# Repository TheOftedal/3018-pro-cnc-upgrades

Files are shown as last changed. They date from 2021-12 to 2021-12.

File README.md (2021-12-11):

# SainSmart Genmitsu 3018-PRO X-Axis Limit Switch

X-axis limiter based on two sub miniature leaf spring switches to sense when the spindle has reached the edge of the x-axis.
This leaves only a couple of millimeters to the edge of the x-axis on either side.
The switches are mounted to the frame with the original M5x16 screws and can thus be fitted with no manipulation of the frame.

## Files

This design consists of two files; x-axis-limit-switch-left and x-axis-limit-switch-right. These pieces are near identical but the right switch has a 2mm longer extrusion to accompany for the stepper motor screws.

## Parts

### Switch

The limit switch holder is designed around a sub miniature leaf spring switch with dimensions of approx. 6.5 x 12.8 x 5.8mm.
Example model that should fit this design: [CYT1073](https://www.amazon.com/Cylewet-25Pcs-Switch-Arduino-CYT1073/dp/B073TYWX86).

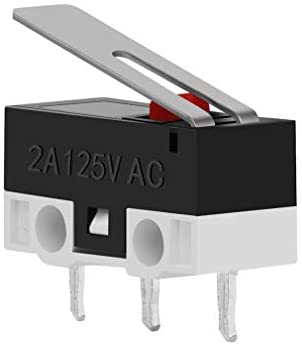
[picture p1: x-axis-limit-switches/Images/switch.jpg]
Switch


### Cables

Any pair of low power cables should suffice for this application.
I do however recommend using a maximum cable dimension of 1.5mm2 to make it easier to solder them onto the micro switch contacts.

### Connectors

The original Genmitsu 3018-PRO control board has a standard dupont pinout for the limit switch connectors and it is therefore recommended to use a dupont crimping tool and 2-pin female connectors to connect the switches to the control board.

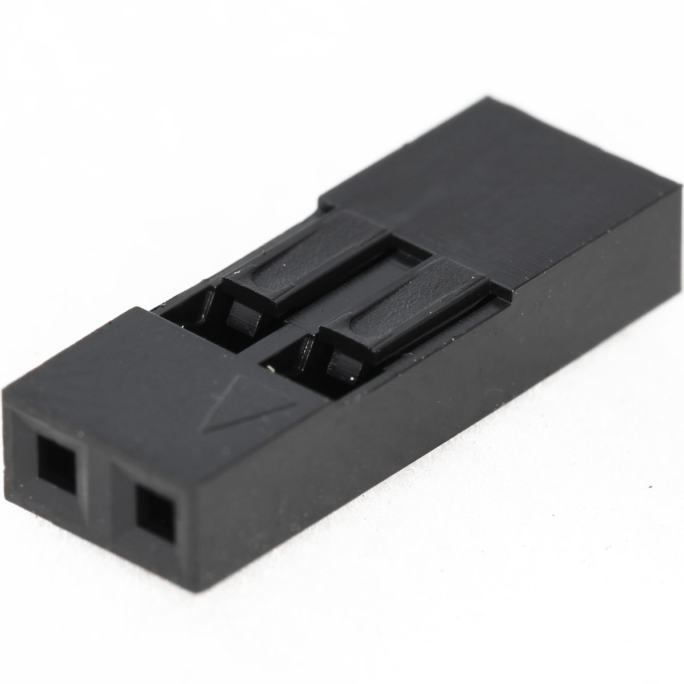
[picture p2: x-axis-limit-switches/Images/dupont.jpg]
Switch


## How to

### Step 1 - 3D-print the holders

Print both 'x-axis-limit-switch-left' and 'x-axis-limit-switch-right' with your choice of printer and filament.

I have successfully printed the design with PLA and with the following settings:

- Extruder Temperature: 230c
- Platform Temperature: 50c
- Layer Height: 0.18mm
- First Layer Height: 0.22mm
- Infill: 15%
- Raft: No
- Supports: No

Due to printing without supports there may be some stringing in the screw holes but this can be easily scraped out with a knife.

### Step 2 - Solder the switches

Solder the cables to the C (Common) and NO (Normally Open) pins of the switch. I recommend to place a small piece of shrink tubing over the solder joints to avoid shortint the pins.

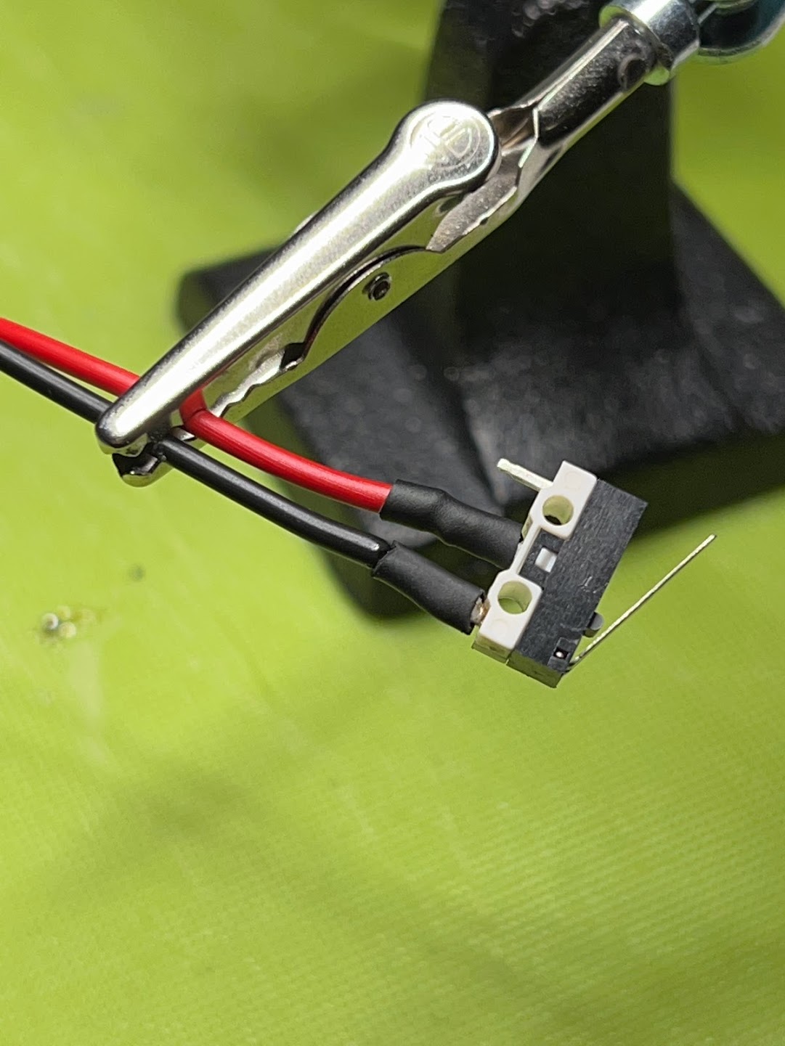
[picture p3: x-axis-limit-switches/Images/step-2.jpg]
Soldering


### Step 3 - Mount the switches to the 3D-printed holders

Fit the cables and switches through the hole of the 3D-printed holders making sure the switch leaf spring is pointing downwards.
The switch should snap into place and be helt snuggly by friction. If the switch is loose, apply some superglue to the switch before fitting it in the socket.

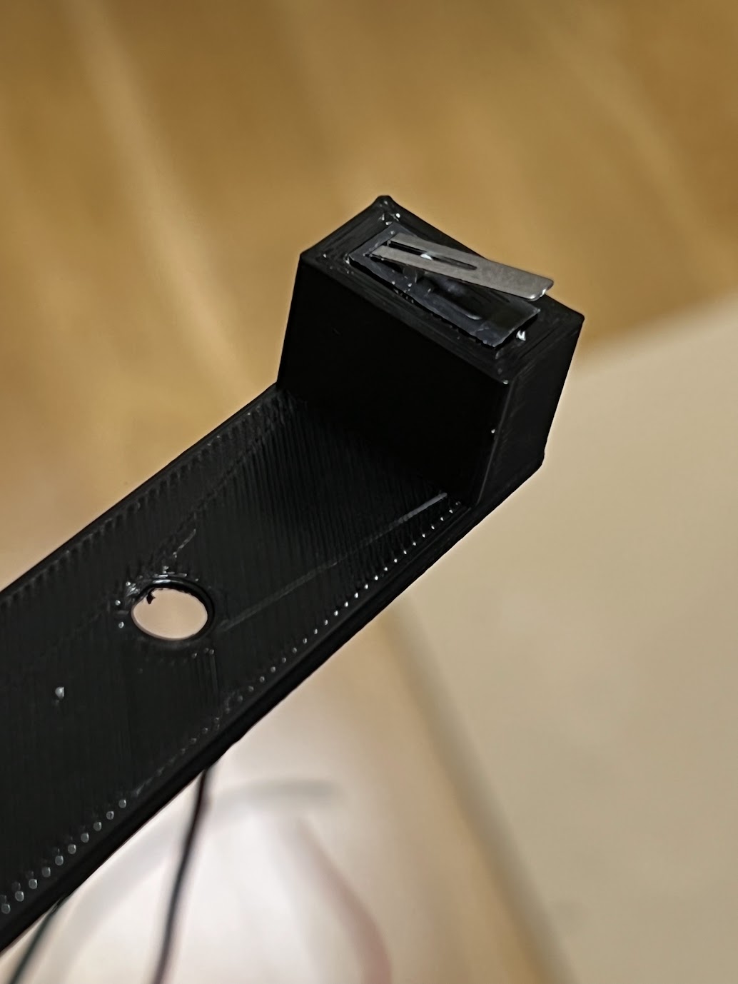
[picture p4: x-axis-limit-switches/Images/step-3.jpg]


### Step 4 - Mount the switches to the frame

Unscrew the middle two bolts holding the bottom guide rail and frame and mount the 3D-printed holders with the switches pointing inwards with the original M5x16mm bolts.

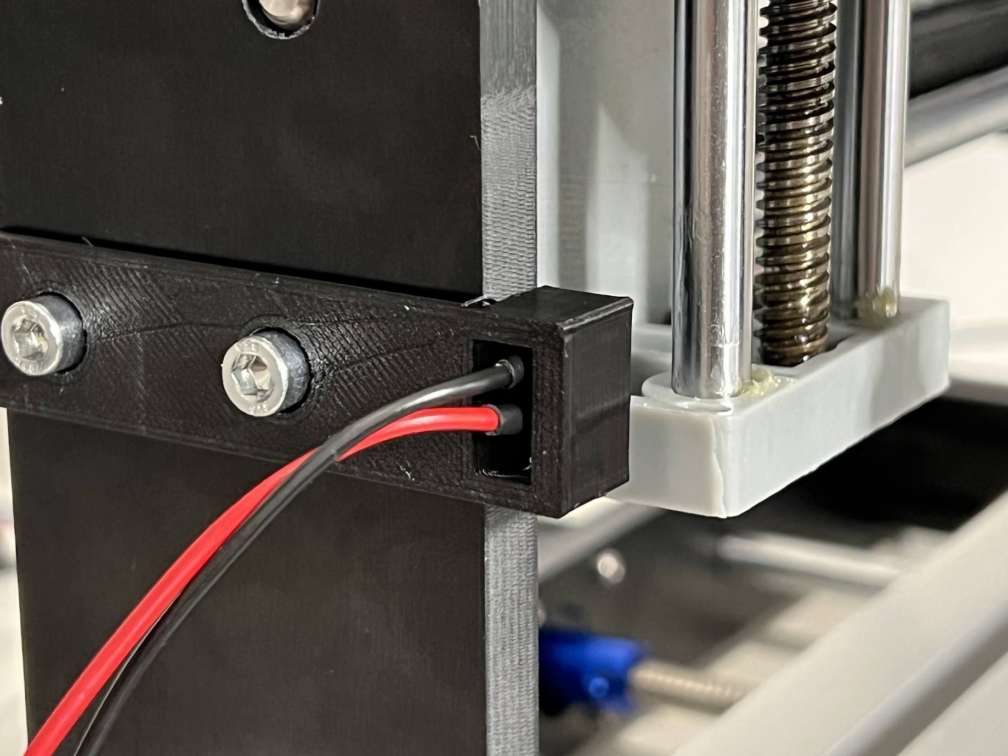
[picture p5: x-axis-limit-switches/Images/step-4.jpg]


## Credits

The micro switch model used for illustration is created by Igor Lirtsman over at [GRABCAD](https://grabcad.com/library/dm1_series-limit-switch-1a-125v-1)

## Like this design?

"Buy Me A Coffee" (https://www.buymeacoffee.com/TheOftedal)

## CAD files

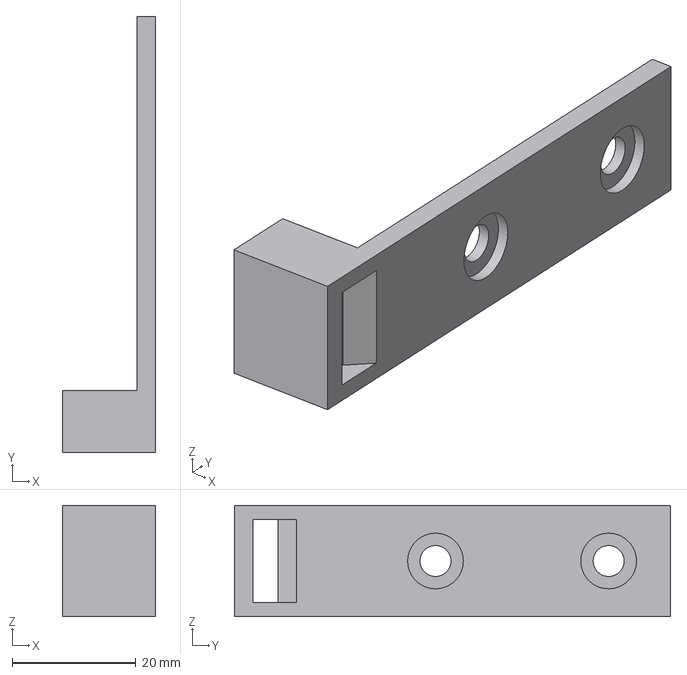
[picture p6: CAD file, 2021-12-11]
x-axis-limit-switches/x-axis-limit-switch-right.stp
15.0 x 70.5 x 18.0 mm

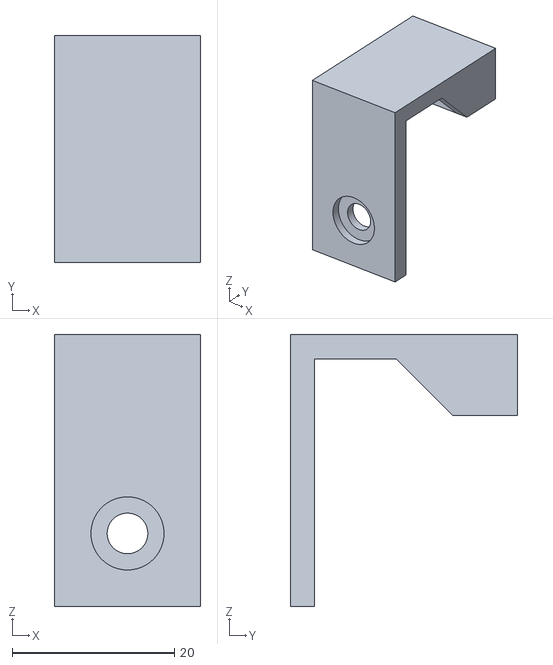
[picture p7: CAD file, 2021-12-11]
y-axis-limit-switches/y-axis-limit-switch-front.stl
18.0 x 28.0 x 33.5

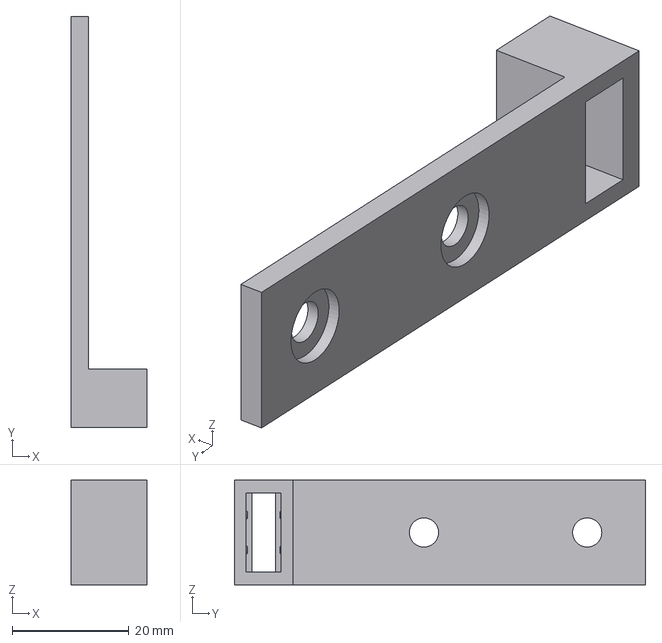
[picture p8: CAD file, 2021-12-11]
x-axis-limit-switches/x-axis-limit-switch-left.stp
13.0 x 70.5 x 18.0 mm

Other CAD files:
x-axis-limit-switches/x-axis-limit-switch-left.stl
x-axis-limit-switches/x-axis-limit-switch-right.stl

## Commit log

2021-12-11 Added first revision of x-axis limit switches
    [x-axis-limit-switch-left.stl, x-axis-limit-switch-left.stp, x-axis-limit-switch-right.stl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]
2021-12-11 Added photos and fixed readme
    [y-axis-limit-switch-front.stl]
